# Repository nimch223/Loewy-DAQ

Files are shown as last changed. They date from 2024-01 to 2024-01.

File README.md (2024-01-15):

# Loewy-DAQ
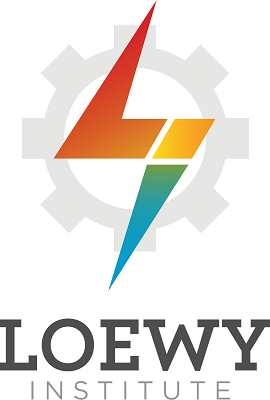
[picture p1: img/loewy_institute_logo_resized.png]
  
Visit our research group website: https://www.lehighloewyinstitute.org  

**Loewy-DAQ** Contains the work of Lehigh University Loewy Institute undergraduate researcher Nicholas Cheney on the development of a chatter monitoring / DAQ system for a 4-high rolling mill. This forms the basis of a project which will be iterated on by future students; the idea is to make use of signal processing in combination with the metal rolling process in order to detect, predict, and respond to incidences of chatter. 

"Guide for Next User" follows, below: 

---
# **Guide for Next User - Vibrational Analysis for a Four-High Rolling Mill**
### **Author**: Nicholas Cheney @nimch223  
### **Advisors**: Professor Wojtek Misiolek & Nick Rockwell @nmrockwell 
### **Document Last Updated On**: January 15, 2024

---

# **Table of Contents:**
+ **[Background](#background)**
+ **[I. Set Up Hardware](#i-set-up-hardware)**  
+ **[II. Download Software: MATLAB & Simulink](#ii-download-software-matlab--simulink)**  
+ **[III. Open & Configure Software](#iii-open--configure-software)**  
+ **[IV. Run Software](#iv-run-software)**  
+ **[V. Additional Information & Future Recommendations](#v-additional-information--future-recommendations)**  
+ **[Papers Referenced](#papers-referenced)**

---

## Background  
Using two ADXL345 accelerometers connected to an Adafruit METRO (a microcontroller that
is equivalent to the Arduino Uno), vibrational analysis of a four high rolling mill can be
performed. The two accelerometers in their housings are to be mounted on the upper backup
roll and top housing of the rolling mill in Whitaker 165.
  
 These two locations for the placement of
the accelerometers were chosen based on a literature review in which it was discovered that
the upper backup roll and top housing demonstrate a higher sensitivity to chatter, making them
ideal locations for the permanent installation of acceleration sensors [Niroomand et al. 864].
  
The accelerometers measure the vertical vibration of the mill for the presence of chatter, the
intense and undesirable vibration of the mill that can negatively impact the rollers and affect
the quality of the rolled material. The most destructive forms of chatter occur at the third and
fifth octave modes of vibration, 100 - 200 Hz and 500 - 700 Hz respectively [Choudhary et al.
1].   

At third octave chatter conditions, the rolled sample experiences poor surface finish quality
and variations in thickness, while at fifth octave chatter conditions the sample experiences
even worse surface finish, larger variations in thickness and potential rupture of the sample,
and the backup and work rolls can experience transverse bending. 

The goal in installing these
vibrational sensors on the rolling mill in Whitaker 165 is to better understand the relationship
between the vibration of a one-stand mill and the quality of rolled samples, and if chatter
occurs, catch it with live vibrational monitoring before it becomes destructive to the sample and
rolls. The following document goes through the process of procuring, manufacturing, and
setting up the hardware for the vibrational sensors, and walks through the steps of how to
configure and run the software for plotting the vibrational data from the two accelerometers. 

--- 

## I. Set Up Hardware  

The following components outline the hardware used to make the vibrational sensor. Included
are either the links of where to find and buy them, or the files where they can be located.  

Files located in Github, at the following location: https://github.com/nimch223/Loewy-DAQ

**1. Microcontroller:**  
- Adafruit METRO 
  - Link: https://www.adafruit.com/product/2488
- Clear Housing for METRO
  - Link: https://www.adafruit.com/product/3597?gad_source=1&gclid=Cj0KCQiAm
4WsBhCiARIsAEJIEzXbmyYK6P6f_sxl3pgHApCRhQQjLrS05EgrbCzs6rN
KPTvZjAyUd0QaAgsNEALw_wcB

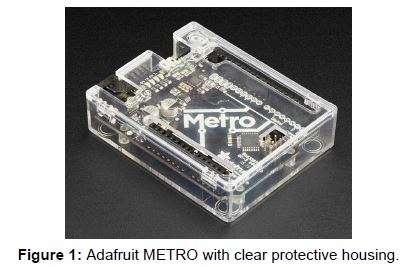
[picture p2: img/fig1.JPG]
  

**2. Accelerometers:**  
- (x2) Adafruit ADXL345 Accelerometers
  - Link: https://www.adafruit.com/product/1231  

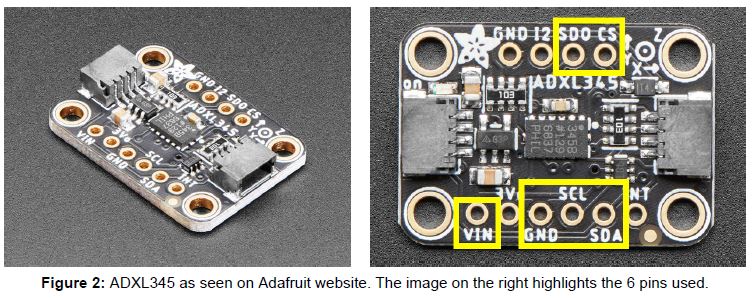
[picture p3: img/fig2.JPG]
   
 
- (x2) 3D-Printed Housing for ADXL345  
  - These housings were designed in SolidWorks to perfectly fit the ADXL345, as no
CAD files could be found online for the current ADXL345 accelerometer model.
Two housings were then printed out of PLA in Wilbur Powerhouse using the FDM
printers.

    - STL File (in this Github repo) for 3D printing: **ADXL345_housing.STL**
    - SolidWorks File (also in this Github repo)--if needed to edit: **ADXL345_housing.SLDPRT**  

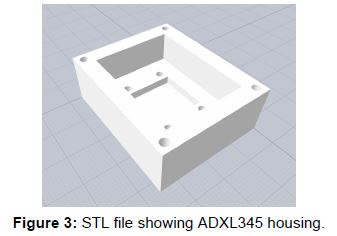
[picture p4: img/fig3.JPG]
  

- (x4) Screws needed to secure each ADXL345 in housing

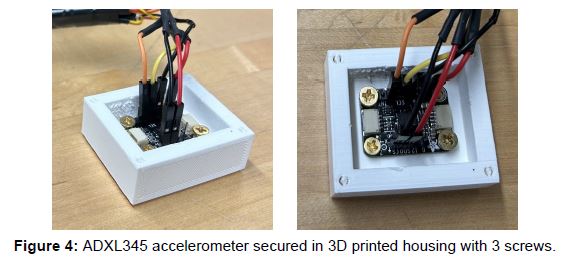
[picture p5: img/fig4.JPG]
    

**3. Printed Circuit Board (PCB):**  
- The PCB was designed in Autodesk EAGLE, a free and intuitive PCB design software.
The physical board was then manufactured in the Electronics Design Lab in Wilbur
Powerhouse using the Othermill V2 CNC Mill. Using the soldering iron in Wilbur, four
10kΩ resistors and break-away male headers were soldered onto the board, shown in
**Figure 6**.

    - Autodesk EAGLE Files (in this Github repository):
      - Schematic File: **PCB_for_ADXL345.sch**  
      - Board File: **PCB_for_ADXL345.brd**

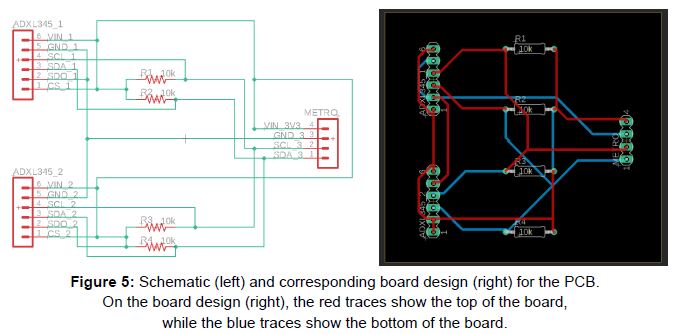
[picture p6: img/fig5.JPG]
  

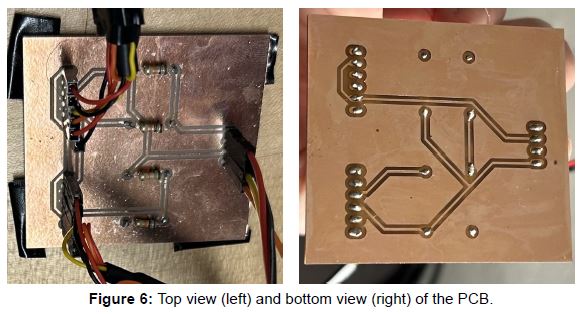
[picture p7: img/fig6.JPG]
  

**4. Wires / Cables:**
- (x4) female-to-male (F/M) jumper wires - used to connect the Arduino to one side of the PCB.
  - These can be seen in **Figure 7**, labeled "3".
    - Link: https://www.adafruit.com/product/1953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

- (x2) female-to-female (F/F) cables.
  - Each cable is roughly 5.5 feet and has 6 female header contacts on each side. Each cable is used to connect the 6 pins on the ADXL345 accelerometer (highlighted in **Figure 2**) to the respective header
on the PCB (labeled "ADXL345_1" and "ADXL345_2" on the schematic in **Figure 5**).
These were spliced and made in the electronics lab in Wilbur Powerhouse.

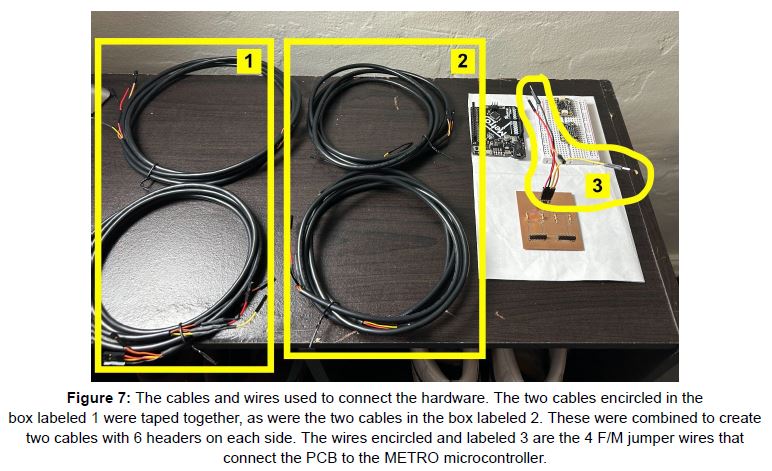
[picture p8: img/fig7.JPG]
  
  
---

## II. Download Software: MATLAB & Simulink  

1. Open the following link: https://matlab.mathworks.com/  
2. Click "Install MATLAB", located at the top right of the page.  
3. Double-click the ".dmg" file that is downloaded onto your ocmputer and follow the steps to finish installation. 
- When asked, install both "MATLAB" and "Simulink". 
- When "Installation Complete" message appears, if prompted, install a supported C compiler for your machine by clicking the link.
  - For Macintosh users, you need at least **Xcode 14.x**
    - For Apple users:
      - Visit https://developer.apple.com/download/more/ and sign into Apple ID.
      - In the search bar, look up "Xcode"
      - Download the most recent version, or the most recent version supported by your machine (for me, Xcode 14.2)
        - Check minimum requirements here: https://developer.apple.com/support/xcode/
      - Launch Xcode, install necessary elements.

---  

## III. Open & Configure Software  

1. Double-click MATLAB to open the program.
2. In the main MATLAB window, search the top toolbar for "Add-Ons" and double-click it to select it. This is highlighted below in **Figure 8**:

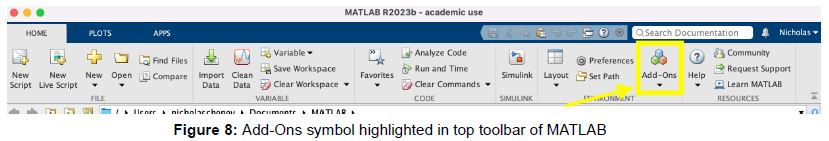
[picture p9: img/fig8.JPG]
  

3. The "Add-On Explorer" window should launch--use the search bar towards the top right, and search for "Arduino".
4. Pluf the microcontroller (METRO / Arduino) into the computer. Ensure it is getting power by making sure the onboard LED is lit.
5. Install the two support packages titled "Simulink Support Package for Arduino Hardware" and "MATLAB Support Package for Arduino Hardware" by clicking the respective titles, and selecting the "Add" blue button on the right side of the screen. Follow the instructions to download, and ensure that the microcontroller is recognized by the computer.
6. Once both support packages have been downloaded, they should have a green "Installed" message by their picture in the "Add-On Explorer", similar to the **Figure 9** below:  

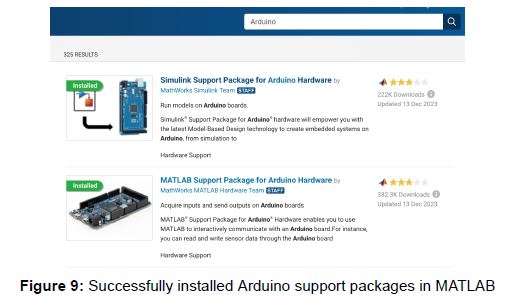
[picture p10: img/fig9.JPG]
  

7. Close the Add-On Explorer window.
8. In the main MATLAB window, search the top toolbar for "Simulink" and double-click it to launch. **Figure 10** below highlights the Simulink symbol in the toolbar:  

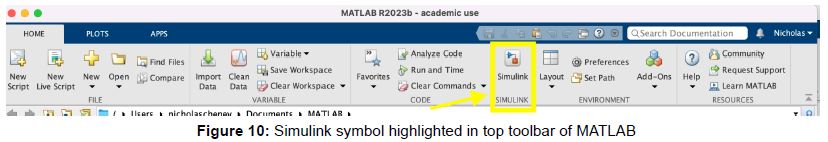
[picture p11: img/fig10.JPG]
  

9. A new Simulink window should open.
10. Download the file titled **"Two_ADXL345_accell.slx"** from Github, and open the file in the Simulink window. The code should appear similar to **Figure 11** below:

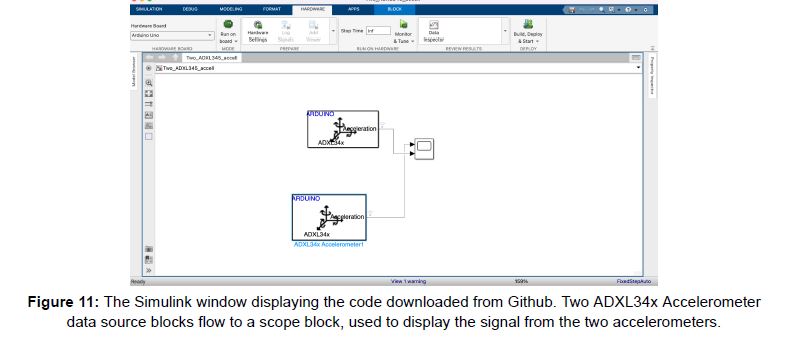
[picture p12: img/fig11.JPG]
  

11. In the Simulink window toolbar, verify that the following settings are configured as follows:
  - Under the "Simulation" tab, set "Stop Time" to "inf" (infinity)
  - Under the "Hardware" tab:
    - Select the "Hardware Board" dropdown menu, and click "Select Another Hardware Board". A "Configuration Parameters" window will appear, and in the "Hardware Implementation" tab, select the "Hardware board:" dropdown meny and select "Arduino Uno". Click "Apply" at the bottom right, then click "OK".
    - Ensure that the mode "Run on board" is selected.
    - Click on "Hardware Settings", and a "Configuration Parameters" window will appear. In the "Hardware Impplementation" tab, select the dropdown menu titled "Target hardware resources" nested in "Hardware board settings". Under the "Groups" ttle, select the "Host-board connection" tab.
    - Open your computer's terminal and type the following command:  
      `ls/vex/tty.*`
      This lists all the serial devices plugged into the computer. The Metro/Arduino should appear as the two serial ports:
      `/dev/tty.SLAB_USBtoUART` and `/dev/tty.usbserial-01C6018D`
      ...the latter, ending with "...018D", is the important one.
    - In the same "Host-board connection" tab, click the dropdown menu for "Set host COM port" and select "Manually select". Directly beneath in the "Host COM Port" dropdown, select `/dev/tty.usbserial-01C6018D/`. Ensure that it is the **`/dev/tty...`** selection and *NOT* the similarly named `/dev/cu...`.
    - Under the same "Groups" title, select the last tab, titled "External mode". Ensure the "Communication interface" dropdown selection is "XCP on Serial".

---  
## IV. Run Software  

1. Navigate back to the MATLAB main window.  
2. Type the following code into the editor window, labeled in Figure 12 below as (1), and then click "Run" labaled as (2):
    
```matlab
% MATLAB commands:
clear all;
clc;
clear a;
a = arduino; 
```

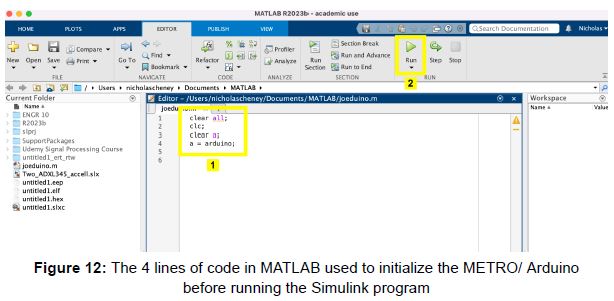
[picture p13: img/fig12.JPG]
  

3. Navigate back to the Simulink window and click "Monitor & Tune" at the top.
4. The code will take some time to run; if it runs successfully, a "Stop" option will appear in the "Hardware" tab of the top toolbar, and "Data Inspector" to the right of it.
5. Click on Data Inspector and a "Simulation Data Inspector" window will appear. Initially, the data coming from the two accelerometers may be displayed on a single graph as 6 lines: "x", "y", and "z" data from each accelerometer.
6. To split the data from the two different accelerometers into two graphs, click the window icon, shown below in Figure 13 as the box highlighted and labeled as (1). Next, under "Basic layouts", select the option with a graph above and below, labeled (2) in **Figure 13** below:

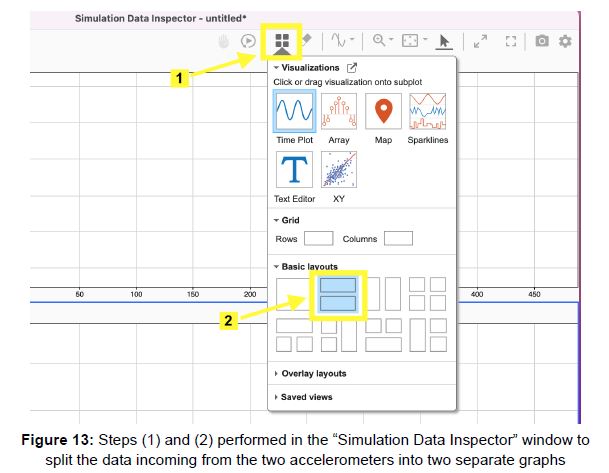
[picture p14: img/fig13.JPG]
  

7. Click the top graph, which is outlined in blue in Figure 14. Under the "Filter signals" dropdown menu on the left, select the checkbox of the 3rd signal from the 1st accelerometer. Ensure that all other signals are deselected. The "Simulation Data Inspector" window should appear in **Figure 14** below:

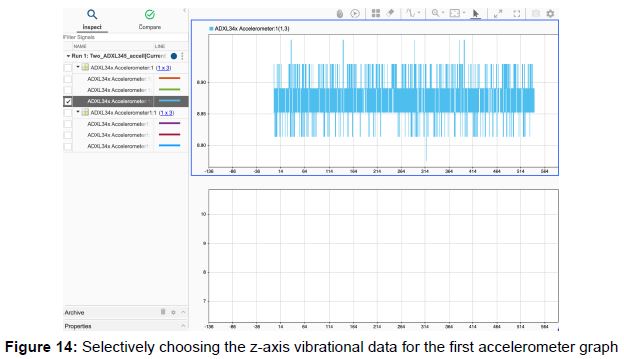
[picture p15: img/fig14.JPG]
  

8. Click the bottom graph, then under the "Filter signals" dropdown menu on the left, select the checkbox of the 3rd signal from the 2nd accelerometer. Ensure that all other signals are deslected. The "Simulation Data Inspector" window should appear like **Figure 15** below:

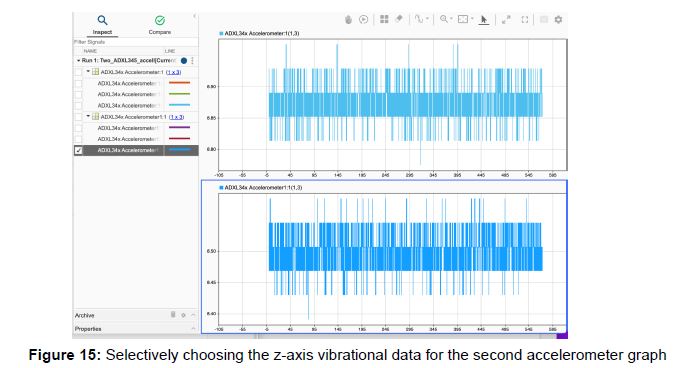
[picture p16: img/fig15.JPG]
  

9. Steps "7" and "8" ensure that only the z-axis (vertical) signal from each accelerometer is graphed. The two running graphs should now display vertical vibrational data from each accelerometer.
10. When finished with measuring the vibrational data, go to the Simulink window and click "Stop" in the toolbar.
11. To save the data from the graphs, go back to the "Simulation Data Inspector" window, and select the "Export" symbol on the left toolbar, shown in **Figure 16** below:

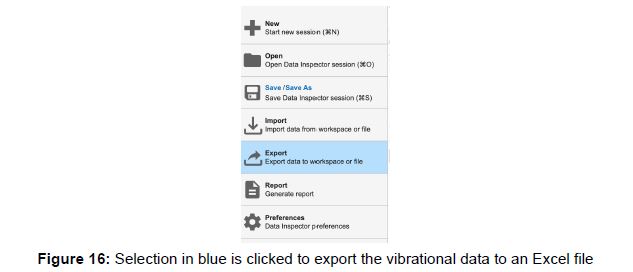
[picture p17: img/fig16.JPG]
  

12. In the "Export" settings window:
    - For "Export:", choose to export only the "Selected runs and signals" for export.
    - For "To:", export the data as an Excel Workbook ".xlsx" file
    - Once the file is exported, the data should appear in your computer under the "MATLAB" folder, wherever that is located.  
  
---  
## V. Additional Information & Future Recommendations  

- The current Simulink code here on Githbu (**Two_ADXL345_accell.slx**) is relatively simple. As displayed in **Figure 11**, it is composed of two accelerometer data source blocks. These blocks are connected to a scope block, which allows for real time data visualization and the real time plotting of the vibrational data.
- These data source blocks are configured so that each block matches the respective I2C address of each accelerometer: **0x1D** and **0x53**.
  - The two accelerometers hooked up in the circuit are recognized under different addresses because one accelerometer's **SDO** pin is connected to **GND**, while the other accelerometer's **SDO** pin is not. This can be seen in **Figure 5** (the PCB schematic).
  - Double-click each accelerometer data source block to display these addresses
  - Double-clicking these blocks also displays additional parameters for the accelerometers that can be set. These parameters include important factors such as the range of acceleration that the accelerometers can measure, and the accelerometer output data rate. *These parameters should be adjusted based on further research and needs*.
  - For example, the accelerometer output data rate is automatically set at 12.5 Hz, which is not high enough for fast and accurate data streaming. The data rate can be adjusted to as high as 1600 Hz.
- This information regarding how the wiring of the pins should be configured in order to communicate with two accelerometers under two different I2C addresses was found in the ADXL345 data sheet. This data sheet, along with the Adafruit ADXL345 website that has pinout, wiring guides, example code, and more, are extremely informative and useful for understanding the capabilities and limitations of the accelerometers. The links are below:
  - ADXL345 Data Sheet: https://www.analog.com/media/en/technical-documentation/data-sheets/adxl345.pdf
 
  - ADXL345 webpage listing: https://learn.adafruit.com/adxl345-digital-accelerometer/overview  

- The need for additional processing, filtering, or denoising of the data may be discovered in the future. The MATLAB and Simulink software was chosen due to it being relatively simple, visual, and intuitive, and an easy base to build off of.
- In order to perform this additional data processing in Simulink, extra blocks would be added to the current Simulink model.
  - Based on the processing needs, pre-built data filtering blocks can be selected from Simulink's library.
  - These filtering blocks can be easily inserted between the accelerometer data source blocks and scope blocks--some examples of filter blocks that can be added are:
    - High pass filter block
    - Automatic gain control block
    - Low pass filter block
  - From the literature review, the aforementioned filters are recommended for data processing [Niroomand et al. 857]. **Figure 17** below shows a potential block diagram for data signal filtering and processing:
 
  
 
  - The process for the ADXL345 accelerometer would be similar to the process shown in **Figure 17** bit slightly different, as the accelerometers have a built in ADC, or "Analog to Digital (A/D) Converter".     
---  

## Papers Referenced  

1. Choudhary et al. “A Review on Chatter Analysis in Cold Rolling process.” Juniper Online
Journal Material Science, vol. 2, issue no. 1, 2017, page 1, ISSN 2575-856X.  

2. Niroomand et al. “Frequency analysis of chatter vibrations in tandem rolling mills.” Journal of
Vibroengineering, vol. 14, issue no. 2, 2012, pages 857 - 864, ISSN 1392-8716.

---

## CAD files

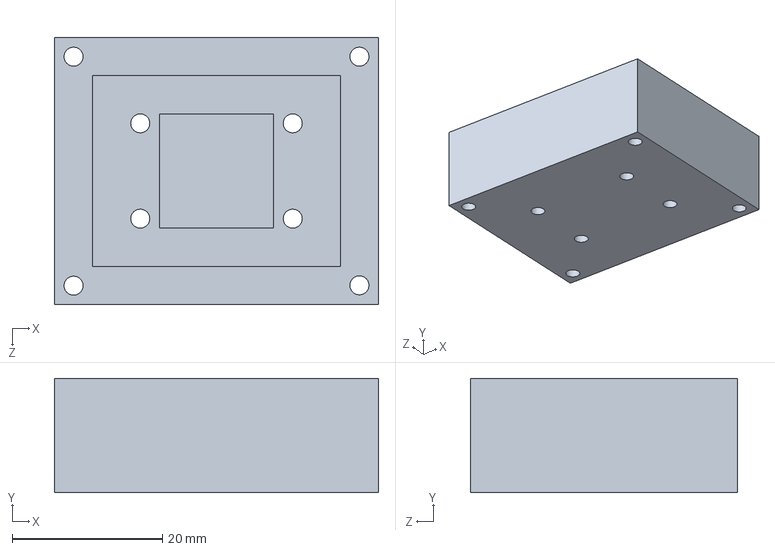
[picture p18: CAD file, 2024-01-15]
ADXL345_housing.SLDPRT
43.2 x 15.2 x 35.6 mm

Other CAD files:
ADXL345_housing.STL

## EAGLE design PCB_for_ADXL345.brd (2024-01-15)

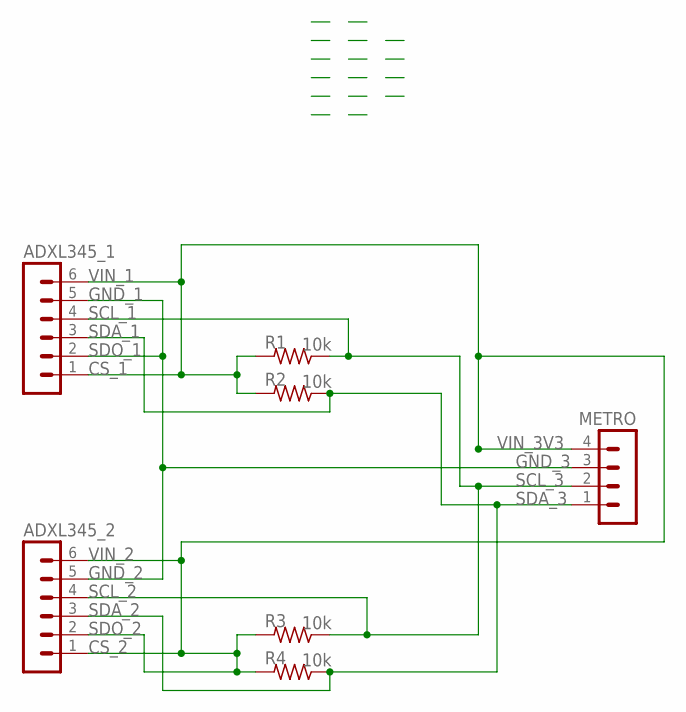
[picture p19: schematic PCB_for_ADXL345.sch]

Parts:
ADXL345_1, ADXL345_2: MA06-1
METRO: MA04-1
R1, R2, R3, R4: 10k; 0207/10

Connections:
GND: ADXL345_1.2, ADXL345_1.5, ADXL345_2.5, METRO.3
unnamed: ADXL345_1.3, ADXL345_2.3, METRO.1, R2.1, R4.1
unnamed: ADXL345_1.4, ADXL345_2.4, METRO.2, R1.1, R3.1
VIN: ADXL345_1.1, ADXL345_1.6, ADXL345_2.1, ADXL345_2.2, ADXL345_2.6, METRO.4, R1.2, R2.2, R3.2, R4.2

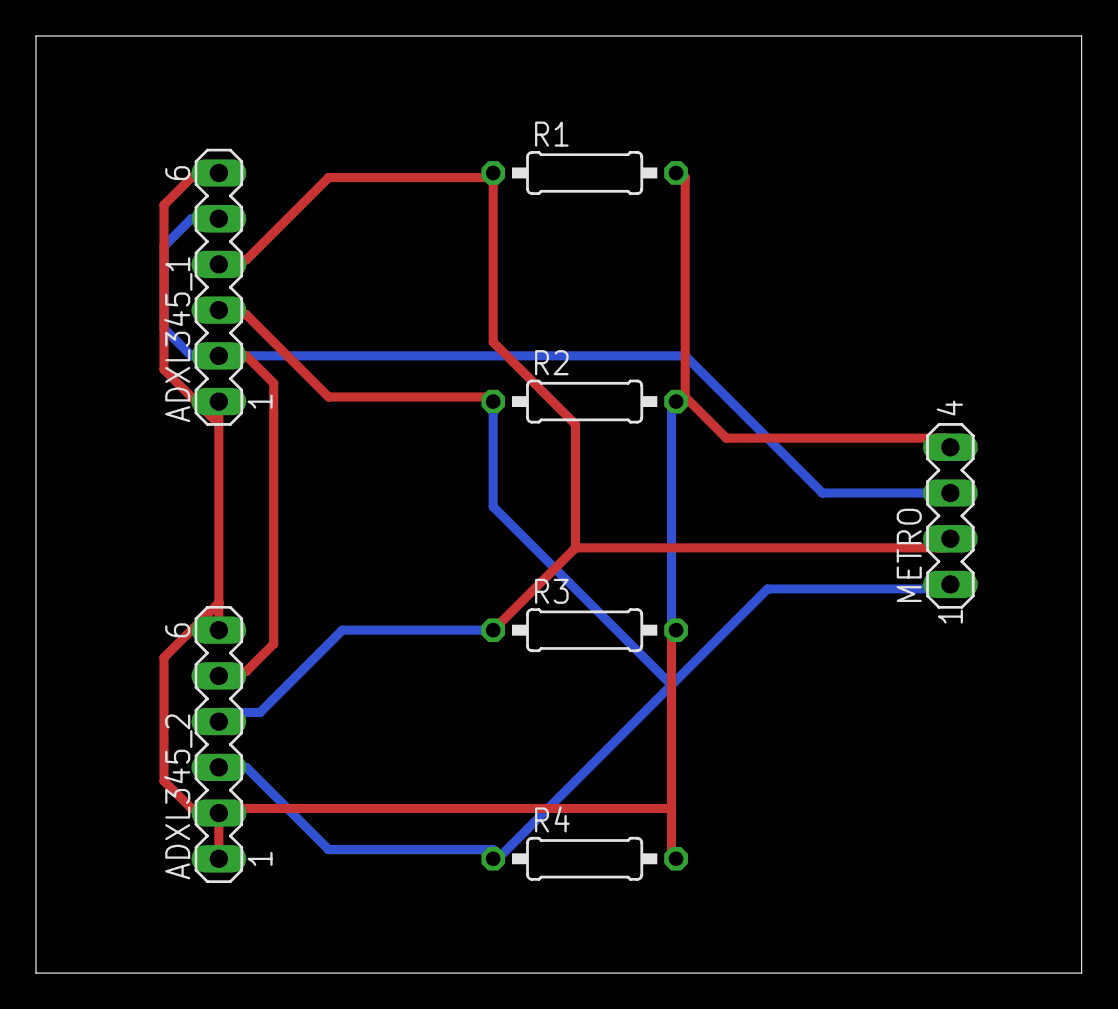
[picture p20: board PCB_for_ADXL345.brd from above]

Board: 2 copper layers, 58.1 x 52.1 mm, 7 parts (0 on the bottom side), 4 nets.
